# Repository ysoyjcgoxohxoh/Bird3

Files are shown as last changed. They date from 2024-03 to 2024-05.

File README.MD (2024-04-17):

# Bird 3 #

## Introduction ##
This repository attempts to document the specs and operation of the Bird 3 scooter. It provides a PCB design and associated software for a drop-in replacement Bird Brain compatible with the EA00004 and EA00022 brains.

The PCB is designed in KiCad around an ESP32-S3. It is designed to fit into the original enclosure and use the existing LCD, the [TXW154028S0](./Datasheets/TXW154028S0_SPEC.pdf).

More documentation for the scooter is available in the [Wiki](../../wiki).

> [!WARNING]
> This repository is intended for use with legally and ethically acquired scooters only. Not only is stealing scooters a crime, it is also unethical.

## Repository Structure ##
- The `Arduino` directory contains the code to run the scooter.
- The `Datasheets` directory contains datasheets for various components.
- The `PCB` directory contains the PCB design.
  - [Rev 1](./PCB/Bird3Controller_Rev1/Readme.md).
  - [Rev 2](./PCB/Bird3Controller_Rev2/Readme.md).
  - [Rev 3](./PCB/Bird3Controller_Rev3/Readme.md).

## Credits ##
- `Mental_Metalhead` - For lots of back and forth testing the software, providing the 22-pin connector pinout, and for various advice on designing PCBs.
- The folks in the Scooterhacking.org community. (DM me if you wish to be credited directly. You know who you are.)

## Board Renderings - Rev 2 ##
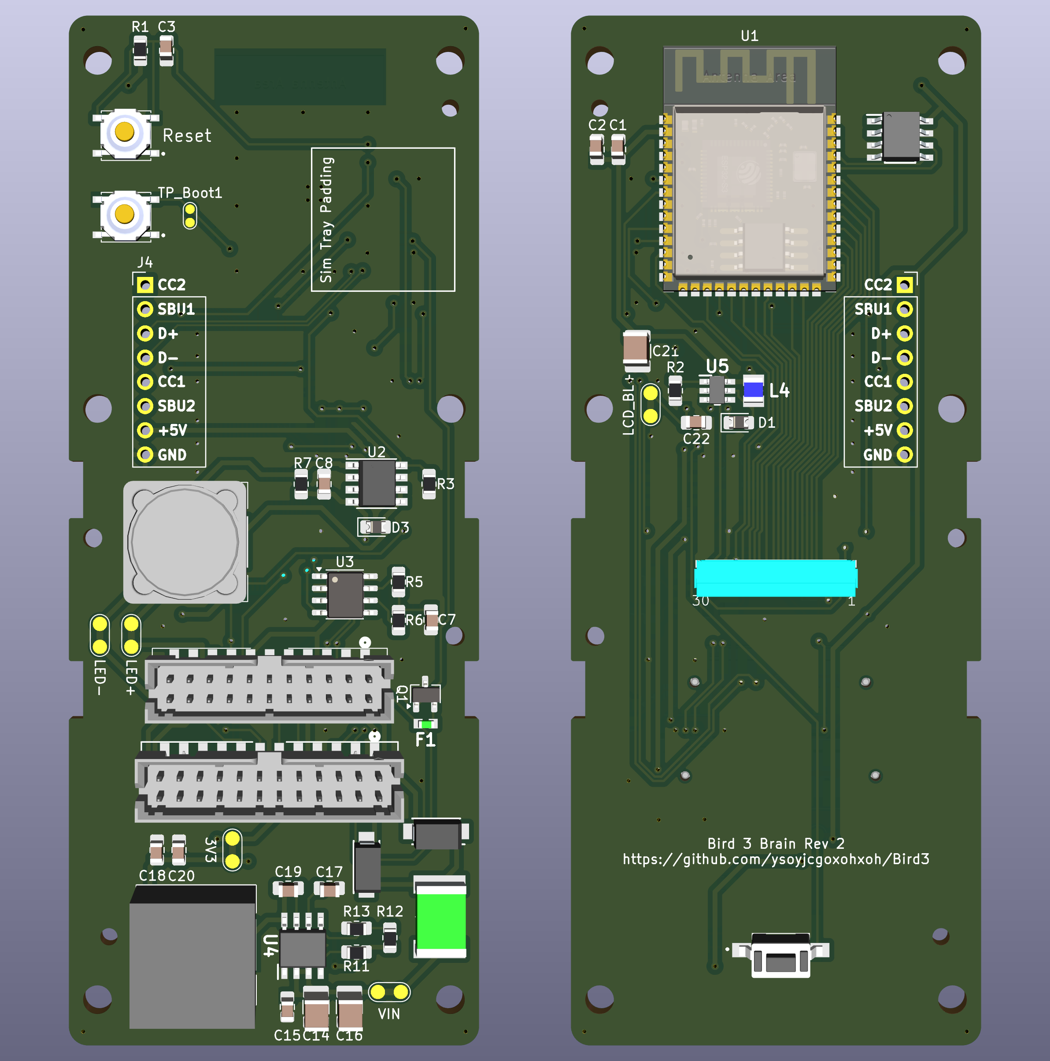
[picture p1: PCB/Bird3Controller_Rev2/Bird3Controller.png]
PCB


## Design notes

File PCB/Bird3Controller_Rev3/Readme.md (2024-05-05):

> [!NOTE]
> This design has been assembled and is working with no errata discovered yet.

## Development ##
This was developed in [KiCad 8](https://www.kicad.org/), a FOSS EDA suite. Most or all of the symbols, footprints, and 3D models have been included in the repo to reduce the chance of broken references.

## Ordering Information ##
[JLCPCB](https://jlcpcb.com/) is a good place from which to order a PCB.
- The gerber files are in the [./plots](plots) folder.
- The Bill of Materials is at [./BOM.csv](BOM.csv).

These JLCPCB settings were used for the order:
| Setting | Value |
|---|---|
| Layers | 2 |
| Dimension | 43 mm * 108 mm |
| PCB Thickness | 1.6 |
| Impedance Control | no |
| Material Type | FR4-Standard TG 135-140 |
| Via Covering | Tented |
| Outer Copper Weight | 1 oz |
| Castellated Holes | no |
| Edge Plating | no |
| Remove Order Number | Specify a location |
| Board Outline Tolerance | ±0.2mm(Regular) |

## Fixes from Rev 2 ##
- TBA

## Improvements from Rev 2 ##
- TBA

## Errata ##
- TBA

## Bill of Materials ##
An interactive BOM generated by [InteractiveHtmlBOM](https://github.com/openscopeproject/InteractiveHtmlBom) is available at [https://html-preview.github.io/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](https://html-preview.github.io/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)

## PDF Schematic ##
A PDF schematic is available at [Bird3Controller.pdf](Bird3Controller.pdf). When opened in a more advanced viewer such as Acrobat Reader, the components are bookmarked, and both components and nets are clickable as shown in this screenshot, making it easy to open the part's datasheet or Mouser.com listing.
PDF Schematic Example

## PNG Schematic ##
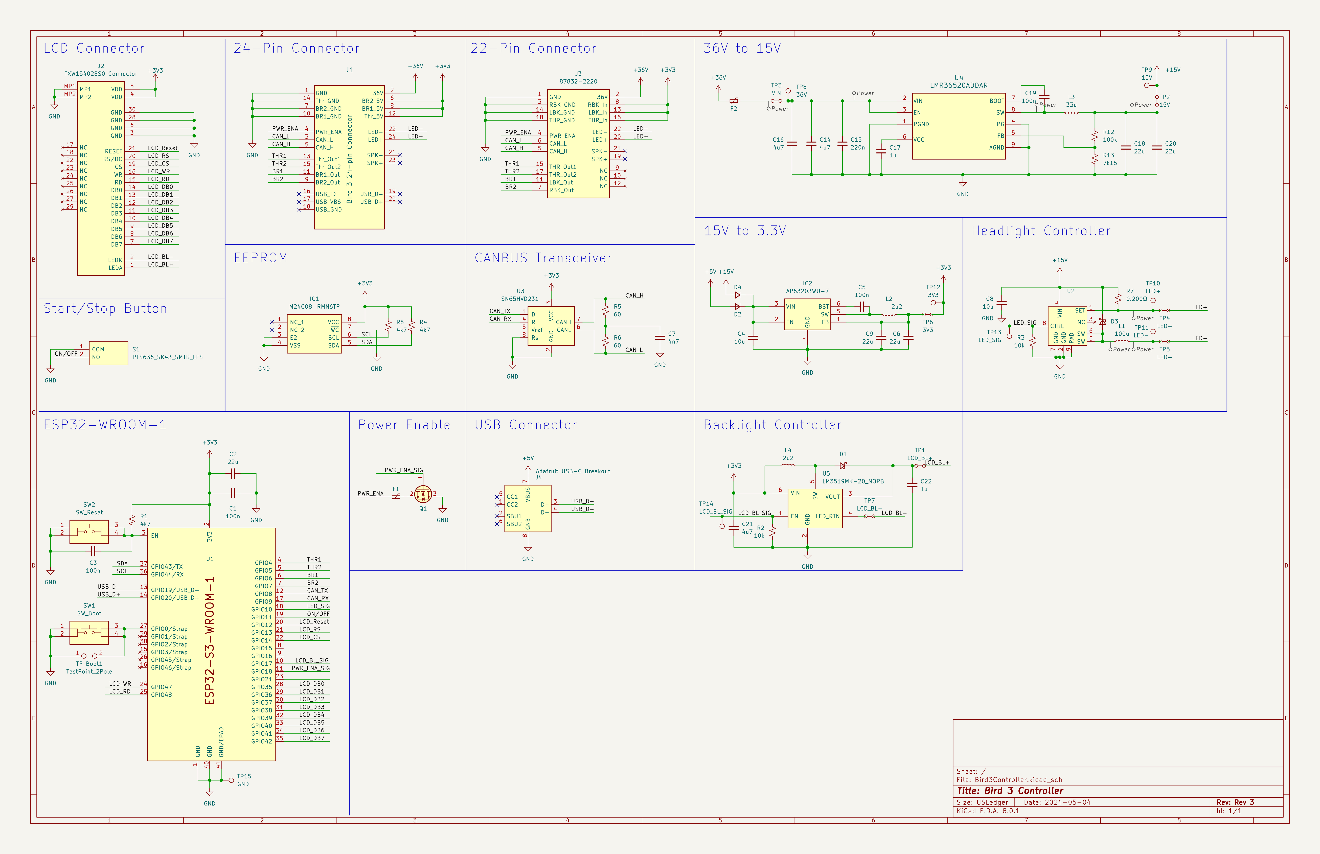
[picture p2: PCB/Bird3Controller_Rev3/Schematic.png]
Schematic


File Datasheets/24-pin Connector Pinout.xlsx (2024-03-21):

Pin Index | Function | Comment | Color
1 | GND | Power Ground | Black
2 | 36V_Perm | Power 36V | Red
3 | CAN_L | CAN Low | Green
4 | PWR_ENA | Ground to Enable Power | Blue
5 | CAN_H | CAN High | Yellow
6 | BR2_5V | Brake 2 Input | Red
7 | BR2_GND | Brake 2 Ground | Black
8 | BR1_5V | Brake 1 Input | Red
9 | BR2_WP | Brake 2 Weak Up | Green
10 | BR1_GND | Brake 1 Ground | Black
11 | BR1_WP | Brake 1 Weak Up | Orange
12 | TR_5V | Throttle Input | Red
13 | TR_WP1 | Throttle Weak Up 1 | Yellow
14 | TR_GND | Throttle Ground | Black
15 | TR_WP2 | Throttle Weak Up 2 | Blue
16 | USB_ID | USB ID | Gray
17 | USB_VBS | USB VBUS | Red
18 | USB_GND | USB Ground | Black
19 | USB_D- | USB D- | White
20 | USB_D+ | USB D+ | Green
21 | SPK- | Speaker Negative | Gray
22 | LED- | LED Negative | White
23 | SPK+ | Speaker Positive | Gray
24 | LED+ | LED Positive | Green

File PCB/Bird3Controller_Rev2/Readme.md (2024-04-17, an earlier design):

> [!NOTE]
> This design doesn't operate the headlight properly.

## Development ##
This was developed in [KiCad 8](https://www.kicad.org/), a FOSS EDA suite. Most or all of the symbols, footprints, and 3D models have been included in the repo to reduce the chance of broken references.

## Ordering Information ##
[JLCPCB](https://jlcpcb.com/) is a good place from which to order a PCB.
- The gerber files are in the [./plots](plots) folder.
- The Bill of Materials is at [./BOM.csv](BOM.csv).

These JLCPCB settings were used for the test order:
| Setting | Value |
|---|---|
| Layers | 2 |
| Dimension | 43 mm* 108 mm |
| PCB Thickness | 1.6 |
| Impedance Control | no |
| Material Type | FR4-Standard TG 135-140 |
| Via Covering | Tented |
| Outer Copper Weight | 1 oz |
| Castellated Holes | no |
| Edge Plating | no |
| Remove Order Number | Specify a location |
| Board Outline Tolerance | ±0.2mm(Regular) |

## Fixes from Rev 1 ##
- Corrected slight inaccuracies in mounting hole locations
- Wired the LCD Connector in the correct direction
- Adjusted LCD mounting to add alignment holes and correct mounting cutout width.
- Moved components interfering with LCD mounting
- Replaced headlight circuit with one that steps down directly from 36V.
- Moved components interfering with LCD
- Increased headlight current setting

## Improvements from Rev 1 ##
- Added 22-pin connector (Credits to `Mental_Metalhead` for the pinout)
- Added EEPROM for durable storage ($0.19 BOM, > 4 million writes)
- Added Mosfet to programatically ground the `PWR_ENA` pin rather than tying it permanently to ground
- Added copper pour to reduce EMI

## Errata ##
- LED Headlight circuit doesn't work due to excessive ratio between VIN (~36V) and VOut (3.0V).

## Board Renderings ##
PCB

## Bill of Materials ##
An interactive BOM generated by [InteractiveHtmlBOM](https://github.com/openscopeproject/InteractiveHtmlBom) is available at [https://html-preview.github.io/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](https://html-preview.github.io/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)

## PDF Schematic ##
A PDF schematic is available at [Bird3Controller.pdf](Bird3Controller.pdf). When opened in a more advanced viewer such as Acrobat Reader, the components are bookmarked, and both components and nets are clickable as shown in this screenshot, making it easy to open the part's datasheet or Mouser.com listing.
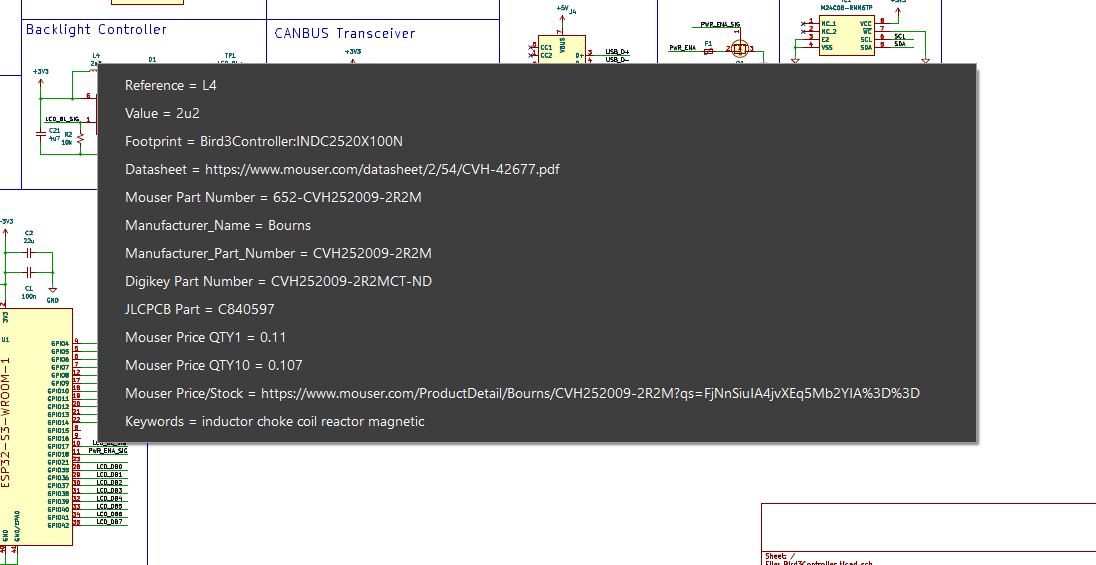
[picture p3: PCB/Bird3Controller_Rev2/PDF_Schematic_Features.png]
PDF Schematic Example


## PNG Schematic ##
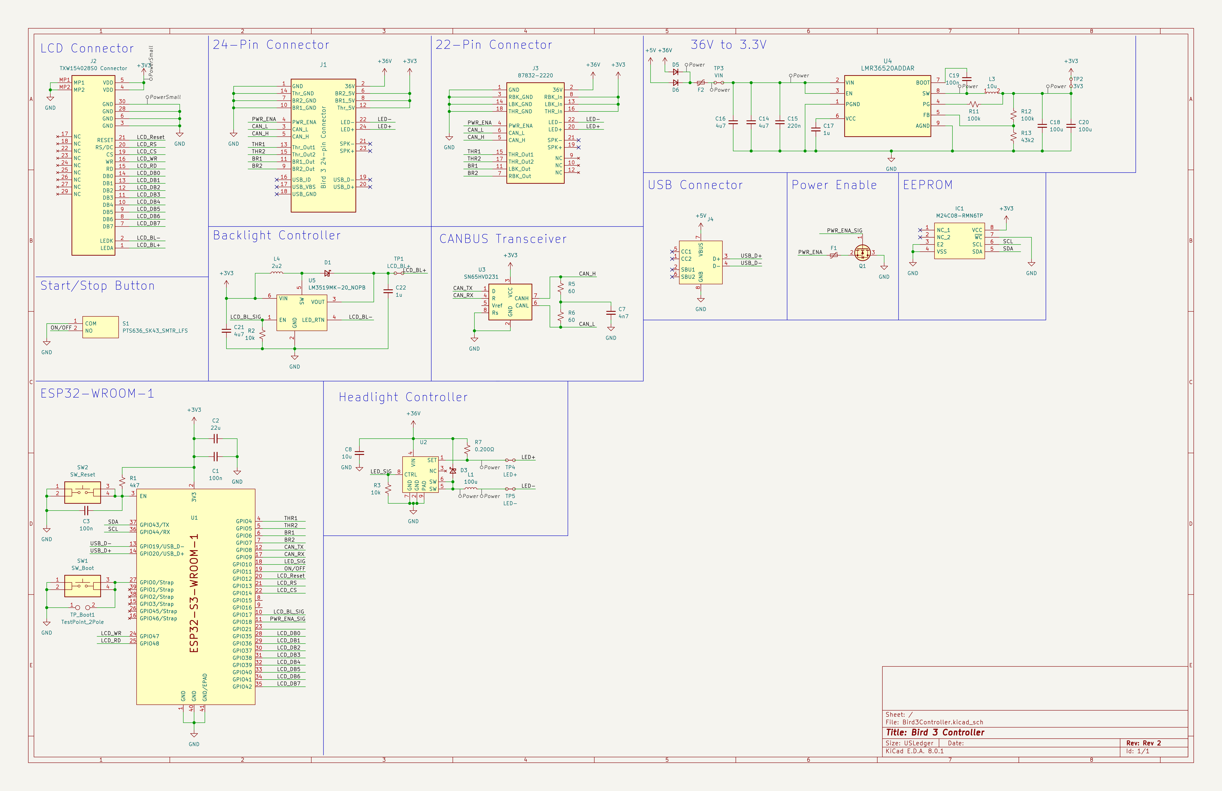
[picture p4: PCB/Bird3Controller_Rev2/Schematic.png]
Schematic


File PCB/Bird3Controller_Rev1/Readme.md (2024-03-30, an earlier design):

> [!NOTE]
> This board does drive the scooter, but it has some issues. This revision is not recommended.

## Errata ##
- Physical
  - The mounting holes are in slightly incorrect locations.
- LCD
  - LCD connector is wired in reverse.
  - The LCD mounting cutouts are not quite big enough, causing a very tight fit when clipping on the LCD.
  - The LCD mounting is missing alignment holes.
  - The data lines to the LCD span two registers, necessitating jumper wires for compatibility with the `TFT_eSPI` library.
- Power
  - There are two 3.3v nets, causing half the board to be unpowered.
  - 3.3v is insufficient for the headlight driver.
- Headlight
  - The headlight driver's current is set too low.
  - The headlight driver's inductor physically interferes with LCD.

## Board Renderings ##
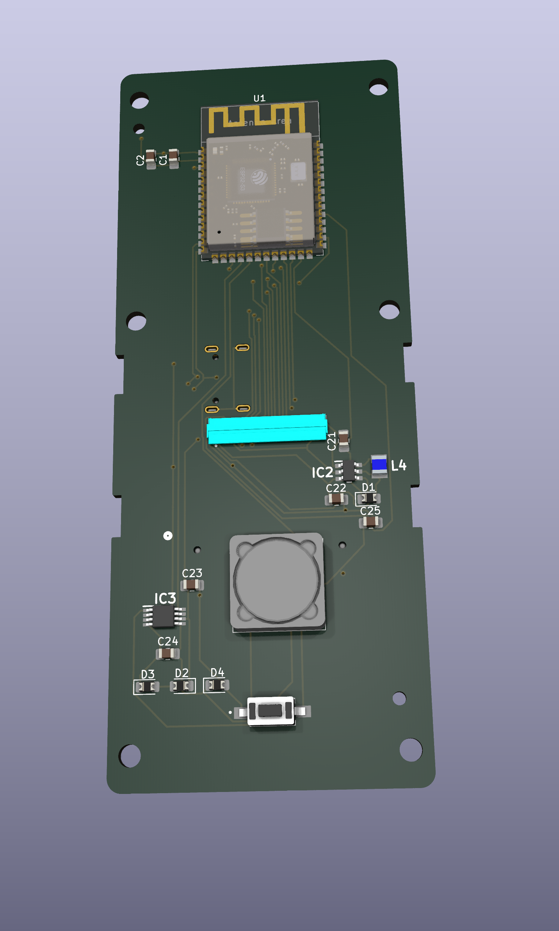
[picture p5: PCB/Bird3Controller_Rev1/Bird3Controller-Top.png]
Top of PCB

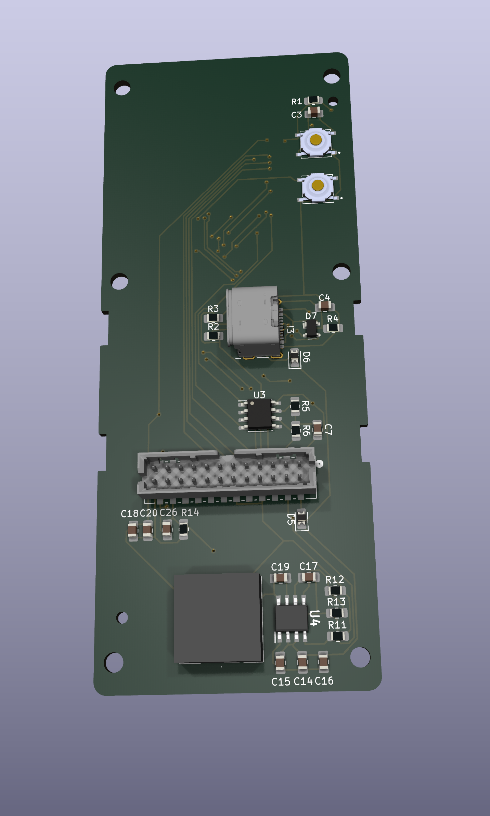
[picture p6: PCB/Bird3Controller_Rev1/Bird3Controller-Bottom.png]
Bottom of PCB


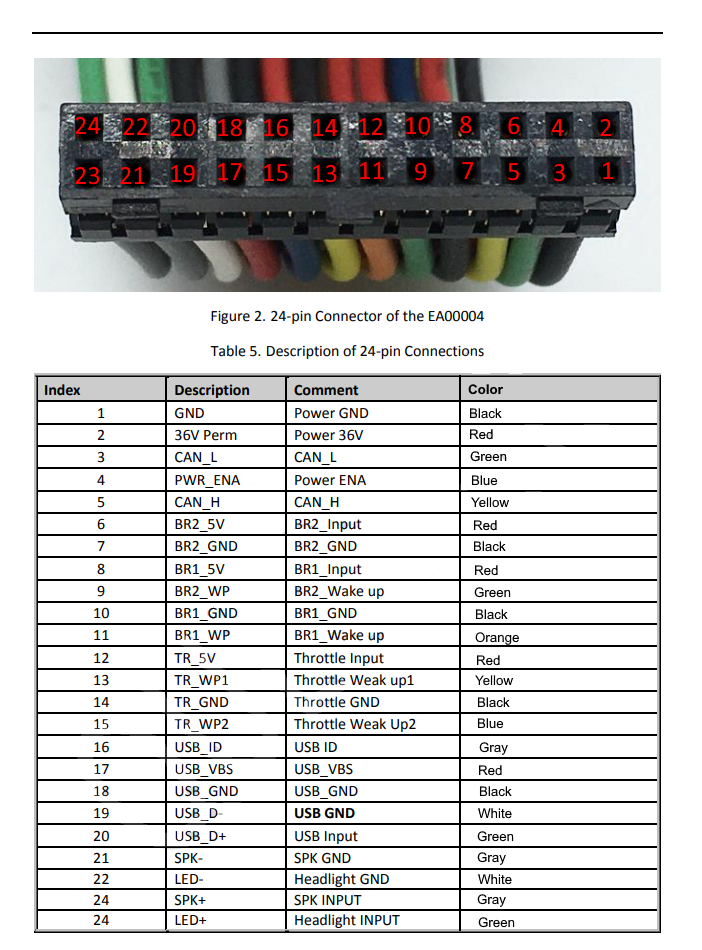
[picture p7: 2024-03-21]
Datasheets/24-pin Connector Pinout.png

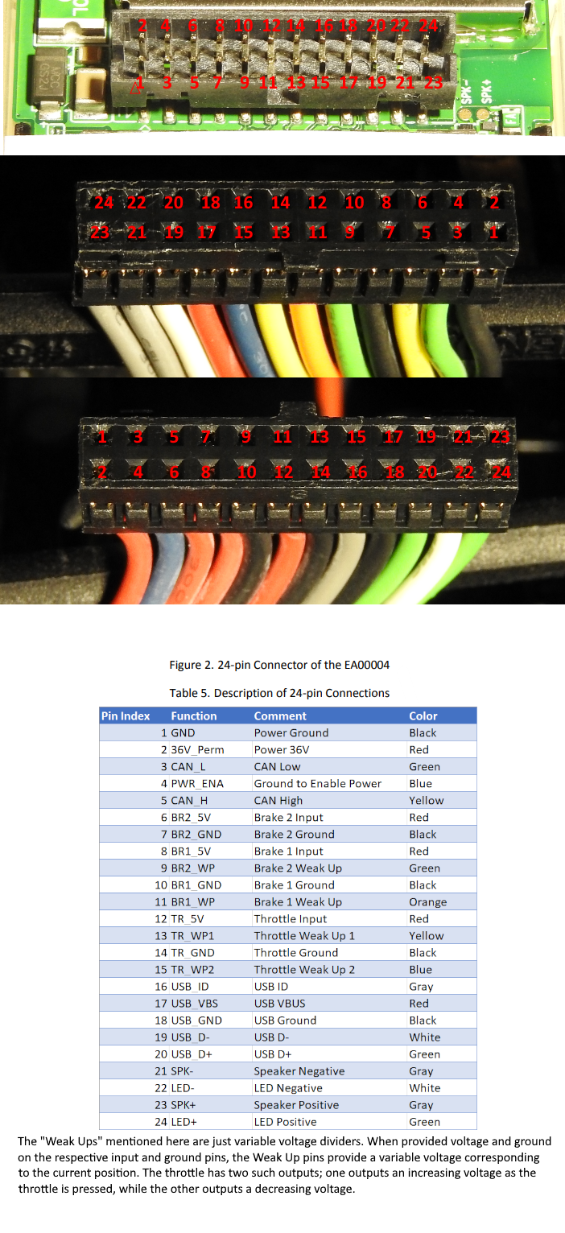
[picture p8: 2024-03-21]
Datasheets/24-pin Connector Pinout Improved.png

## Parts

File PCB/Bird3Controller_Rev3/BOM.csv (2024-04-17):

Reference | Value | Rating | Description | Manufacturer_Name | Manufacturer_Part_Number | Mouser Part Number | Mouser Price/Stock | Qty | Mouser Price QTY1 | Mouser Price QTY10
C1,C3,C5,C19 | 100n | 50V | -- mixed values -- | YAGEO | AC0805JRX7R9BB104 | 603-AC0805JX7R9BB104 | https://www.mouser.com/ProductDetail/YAGEO/AC0805JRX7R9BB104?qs=Znm5pLBrcAKKHbaCmv3b8Q%3D%3D | 4 | 0.10 | 0.065
C2 | 22u | 16V | ESP32 Decoupling | Murata Electronics | GRT21BR61C226ME13L | 81-GRT21BR61C226ME3L | https://www.mouser.com/ProductDetail/Murata-Electronics/GRT21BR61C226ME13L?qs=drgMNd%252BkGPOXePTBixOAtw%3D%3D | 1 | 0.39 | 0.196
C4,C8 | 10u | 25V | 5V/15V Decoupling | Murata Electronics | GRT21BC71E106KE13L | 81-GRT21BC71E106KE13 | https://www.mouser.com/ProductDetail/Murata-Electronics/GRT21BC71E106KE13L?qs=rrS6PyfT74dm3CAfGBwgnw%3D%3D | 2 | 0.35 | 0.199
C6,C9 | 22u | 6.3V | 3V3 Output Filtering | Samsung Electro-Mechanics | CL21A226MQQNNNE | 187-CL21A226MQQNNNE | https://www.mouser.com/ProductDetail/Samsung-Electro-Mechanics/CL21A226MQQNNNE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 | 2 | 0.13 | 0.053
C7 | 4n7 | 50V | CANBUS Split Termination | KYOCERA AVX | 08055C472K4T4A | 581-08055C472K4T4A | https://www.mouser.com/ProductDetail/KYOCERA-AVX/08055C472K4T4A?qs=ykEKLGTiBcx6ErrkugvmMg%3D%3D | 1 | 0.10 | 0.058
C14,C16,C21 | 4u7 | 50V | -- mixed values -- | Samsung Electro-Mechanics | CL32Y475MCIVPNE | 187-CL32B475KBUYNNE | https://www.mouser.com/ProductDetail/Samsung-Electro-Mechanics/CL32B475KBUYNNE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 | 3 | 0.36 | 0.179
C15 | 220n | 50V | 36V Decoupling | Samsung Electro-Mechanics | CL21B224KBFNNNG | 187-CL21B224KBFNNNG | https://www.mouser.com/ProductDetail/Samsung-Electro-Mechanics/CL21B224KBFNNNG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 | 1 | 0.10 | 0.02
C17,C22 | 1u | 50V | LCD Backlight Output Cap | Samsung Electro-Mechanics | CL21B105MBFNNNE | 187-CL21B105MBFNNNE | https://www.mouser.com/ProductDetail/Samsung-Electro-Mechanics/CL21B105MBFNNNE?qs=Znm5pLBrcAIRYa0zX3s5Qw%3D%3D | 2 | 0.10 | 0.027
C18,C20 | 22u | 25V | 15V Output Cap | Samsung Electro-Mechanics | CL21A226MAYNNNE | 187-CL21A226MAYNNNE | https://www.mouser.com/ProductDetail/Samsung-Electro-Mechanics/CL21A226MAYNNNE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 | 2 | 0.25 | 0.115
D1,D3 | D_Schottky_Small | 20V | Freewheeling Diode | KYOCERA AVX | SD0805S020S1R0 | 581-SD0805S020S1R0 | https://www.mouser.com/ProductDetail/KYOCERA-AVX/SD0805S020S1R0?qs=jCA%252BPfw4LHbpkAoSnwrdjw%3D%3D | 2 | 0.32 | 0.252
D2,D4 | GS1J_R1_00001 | 600V | 15V input diode | PANJIT | GS1J_R1_00001 | 241-GS1J_R1_00001 | https://www.mouser.com/ProductDetail/Panjit/GS1J_R1_00001?qs=sPbYRqrBIVmiablUMOUd0Q%3D%3D | 2 | 0.21 | 0.148
F1 | Polyfuse_Small | 60V | PWR_ENA Fuse | Bel Fuse | 0ZCM0001FF2G | 530-0ZCM0001FF2G | https://www.mouser.com/ProductDetail/Bel-Fuse/0ZCM0001FF2G?qs=uwxL4vQweFOSr3rpPGffpA%3D%3D | 1 | 0.19 | 0.16
F2 | 0ZCF0100AF2A | 60V | VIN Fuse | BelFuse | 0ZCF0100AF2A | 530-0ZCF0100AF2A | https://www.mouser.com/ProductDetail/Bel-Fuse/0ZCF0100AF2A?qs=jyPKP7YLNfDyY7GbSCl%252BVQ%3D%3D | 1 | 0.55 | 0.454
IC1 | M24C08-RMN6TP | 5.5V | EEPROM | STMicroelectronics | M24C08-RMN6TP | 511-M24C08-RMN6TP | https://www.mouser.com/ProductDetail/STMicroelectronics/M24C08-RMN6TP?qs=%252B9pWl1iD4MWbThyGTUpSoQ%3D%3D | 1 | 0.19 | 0.175
IC2 | AP63203WU-7 | 32V | 3V3 Switching Regulator | Diodes Incorporated | AP63203WU-7 | 621-AP63203WU-7 | https://www.mouser.com/ProductDetail/Diodes-Incorporated/AP63203WU-7?qs=u16ybLDytRZ1JqxbuLkMJw%3D%3D | 1 | 0.87 | 0.71
J1 | Bird 3 24-pin Connector | 125V, 2A | 24-Pin Connector | Molex | 87832-6123 | 538-87832-6123 | https://www.mouser.com/ProductDetail/Molex/87832-6123?qs=Vr3ZXvgdfhaw8VVGfNJm1w%3D%3D | 1 | 2.05 | 1.79
J2 | TXW154028S0 Connector | 50V, 125mA | LCD Connector | Hirose | FH34SRJ-30S-0.5SH(50) | 798-FH34SRJ30S05SH50 | https://www.mouser.com/ProductDetail/Hirose-Connector/FH34SRJ-30S-0.5SH50?qs=vnk2wBG9e16HHwHqXDE2%252Bg%3D%3D | 1 | 1.24 | 1.05
J3 | 87832-2220 | 125V, 2A | 22-Pin Connector | Molex | 87832-6062 | 538-87832-6062 | https://www.mouser.com/ProductDetail/Molex/87832-6062?qs=yd8XiKYcH9k38KQb4jjFuQ%3D%3D | 1 | 3.27 | 2.98
J4 | Adafruit USB-C Breakout |  | USB-C Breakout | Adafruit | 4090 | 485-4090 | https://www.mouser.com/ProductDetail/Adafruit/4090?qs=2WXlatMagcFDROXrdbBXdg%3D%3D | 1 | 2.95 | 2.95
L1 | 100u | 1.2A, 300mOhms | Headlight Inductor | Bourns | SRR1240-101M | 652-SRR1240-101M | https://www.mouser.com/ProductDetail/Bourns/SRR1240-101M?qs=y9m3SKnhpLNdXTkYqTD5yw%3D%3D | 1 | 0.64 | 0.634
L2 | 2u2 | 2.2A, 90mOhms | 3.3V Inductor | TAIYO YUDEN | MAMK2520H2R2M | 963-MAMK2520H2R2M | https://www.mouser.com/ProductDetail/TAIYO-YUDEN/MAMK2520H2R2M?qs=4JX4e57RtWy63Hw12ZxQ0w%3D%3D | 1 | 0.23 | 0.158
L3 | 33u | 4A, 127.6mOhms | 15V Inductor | Bourns | SRP7050WA-330M | 652-SRP7050WA-330M | https://www.mouser.com/ProductDetail/Bourns/SRP7050WA-330M?qs=9vOqFld9vZUZDPDePm2oBQ%3D%3D | 1 | 0.88 | 0.757
L4 | 2u2 | 1.3A, 80mOhms | Backlight Inductor | Bourns | CVH252009-2R2M | 652-CVH252009-2R2M | https://www.mouser.com/ProductDetail/Bourns/CVH252009-2R2M?qs=FjNnSiuIA4jvXEq5Mb2YIA%3D%3D | 1 | 0.11 | 0.107
Q1 | 2N7002A | 60V, 280mA, 2 Ohms | PWR_ENA Transistor | Diotec | 2N7002A | 637-2N7002A | https://www.mouser.com/ProductDetail/Diotec-Semiconductor/2N7002A?qs=OlC7AqGiEDkkJvTsYoVAvg%3D%3D | 1 | 0.11 | 0.081
R1,R4,R8 | 4k7 | 150v, 125mW | -- mixed values -- | Vishay / Dale | CRCW08054K70JNEA | 71-CRCW0805J-4.7K-E3 | https://www.mouser.com/ProductDetail/Vishay-Dale/CRCW08054K70JNEA?qs=kkyyugUlSrPc3tCn%2F8R5yw%3D%3D | 3 | 0.10 | 0.02
R2,R3 | 10k | 150v, 125mW | -- mixed values -- | Vishay / Dale | CRCW080510K0JNEA | 71-CRCW0805J-10K-E3 | https://www.mouser.com/ProductDetail/Vishay-Dale/CRCW080510K0JNEA?qs=LOX6nxTstiZtNB6HA62jyQ%3D%3D | 2 | 0.10 | 0.019
R5,R6 | 60 | 150v, 500mW | CANBUS Termination | Vishay / Dale | RCS080560R4FKEA | 71-RCS080560R4FKEA | https://www.mouser.com/ProductDetail/Vishay-Dale/RCS080560R4FKEA?qs=AAB0DUhlpksv20rhg0ZRxw%3D%3D | 2 | 0.13 | 0.043
R7 | 0.200Ω | 125mW | Current Sense | TE Connectivity / CGS | RLC73K2AR20FTDF | 279-RLC73K2AR20FTDF | https://www.mouser.com/ProductDetail/TE-Connectivity-CGS/RLC73K2AR20FTDF?qs=9vOqFld9vZWQ3oqbYNtegw%3D%3D | 1 | 0.26 | 0.221
R12 | 100k | 150v, 500mW | 15V Voltage Set Divider | Vishay / Dale | RCS0805100KFKEA | 71-RCS0805100KFKEA | https://www.mouser.com/ProductDetail/Vishay-Dale/RCS0805100KFKEA?qs=NKmfXavxMay%252BH0mbX9hKBw%3D%3D | 1 | 0.13 | 0.063
R13 | 7k15 | 150v, 500mW | 15V Voltage Set Divider | Vishay / Dale | CRCW08057K15FKEAC | 71-CRCW08057K15FKEAC | https://www.mouser.com/ProductDetail/Vishay-Dale/CRCW08057K15FKEAC?qs=E3Y5ESvWgWMF1asUDdVWEg%3D%3D | 1 | 0.11 | 0.029
S1 | PTS636_SK43_SMTR_LFS | 12V, 50mA | Start/Stop Button | C & K COMPONENTS | PTS636 SK43 SMTR LFS | 611-PTS636SK43SMTRLF | https://www.mouser.com/ProductDetail/CK/PTS636-SK43-SMTR-LFS?qs=vLWxofP3U2wsQpQ593zsYw%3D%3D | 1 | 0.16 | 0.148
SW1,SW2 | -- mixed values -- | 12V, 50mA | -- mixed values -- | C & K COMPONENTS | PTS526 SK15 SMTR2 LFS | 611-PTS526SK15SMR2L | https://www.mouser.com/ProductDetail/CK/PTS526-SK15-SMTR2-LFS?qs=UXgszm6BlbF5Ezp94JAQtw%3D%3D | 2 | 0.14 | 0.13
TP8,TP9,TP10,TP11,TP12,TP13,TP14,TP15 | -- mixed values -- |  | test point |  |  |  |  | 8
U1 | ESP32-S3-WROOM-1 | 3.6V | Microcontroller | Espressif Systems | ESP32-S3-WROOM-1-N8R8 | 356-EP32S3WROOM1N8R8 | https://www.mouser.com/ProductDetail/Espressif-Systems/ESP32-S3-WROOM-1-N8R8?qs=7D1LtPJG0i3%2F28hKFavOpQ%3D%3D | 1 | 3.62 | 3.62
U2 | ~ | 60V | Headlight Driver | Diodes | AL8862SP-13 | 621-AL8862SP-13 | https://www.mouser.com/ProductDetail/Diodes-Incorporated/AL8862SP-13?qs=W0yvOO0ixfFVclRYoOMX8w%3D%3D | 1 | 0.93 | 0.748
U3 | SN65HVD231 | 3.6V | CANBUS Driver | Texas Instruments | SN65HVD231DRG4 | 595-SN65HVD231DRG4 | https://www.mouser.com/ProductDetail/Texas-Instruments/SN65HVD231DRG4?qs=QViXGNcIEAtYBoUJPHGedA%3D%3D | 1 | 2.51 | 2.25
U4 | LMR36520ADDAR | 65V | 15V Switching Regulator | Texas Instruments | LMR36520ADDAR | 595-LMR36520ADDAR | https://www.mouser.com/ProductDetail/Texas-Instruments/LMR36520ADDAR?qs=vHuUswq2%252Bsxe%2FiIOFannaw%3D%3D | 1 | 2.72 | 2.39
U5 | LM3519MK-20_NOPB | 5.5V | Backlight Driver | Texas Instruments | LM3519MK-20/NOPB | 926-LM3519MK-20/NOPB | https://www.mouser.com/ProductDetail/Texas-Instruments/LM3519MK-20-NOPB?qs=QbsRYf82W3GbfCEf8%2FkE2A%3D%3D | 1 | 2.02 | 1.72

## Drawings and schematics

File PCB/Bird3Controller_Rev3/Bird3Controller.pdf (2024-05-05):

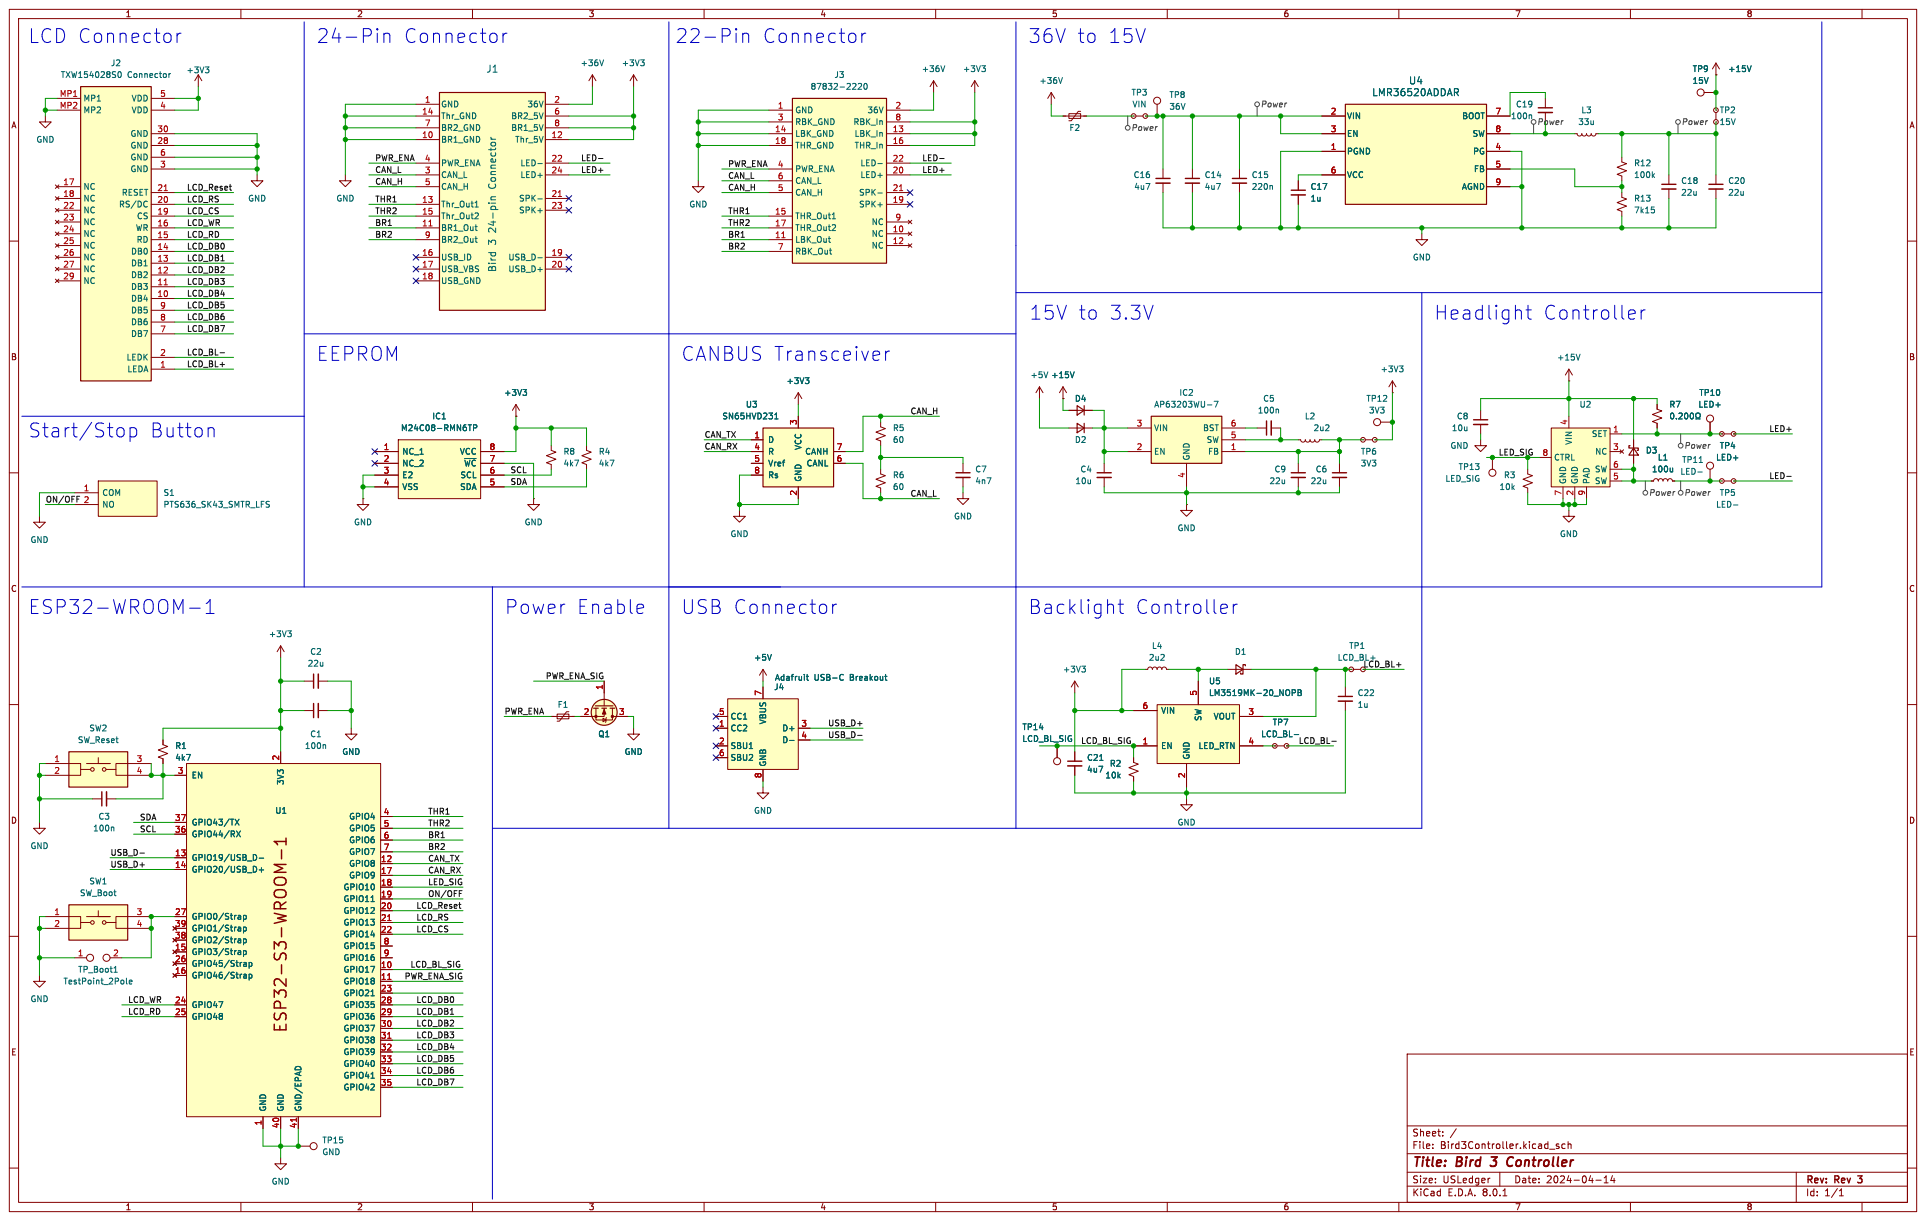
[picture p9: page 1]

Id: 1/1 Title: Bird 3 Controller File: Bird3Controller.kicad_sch Sheet: /

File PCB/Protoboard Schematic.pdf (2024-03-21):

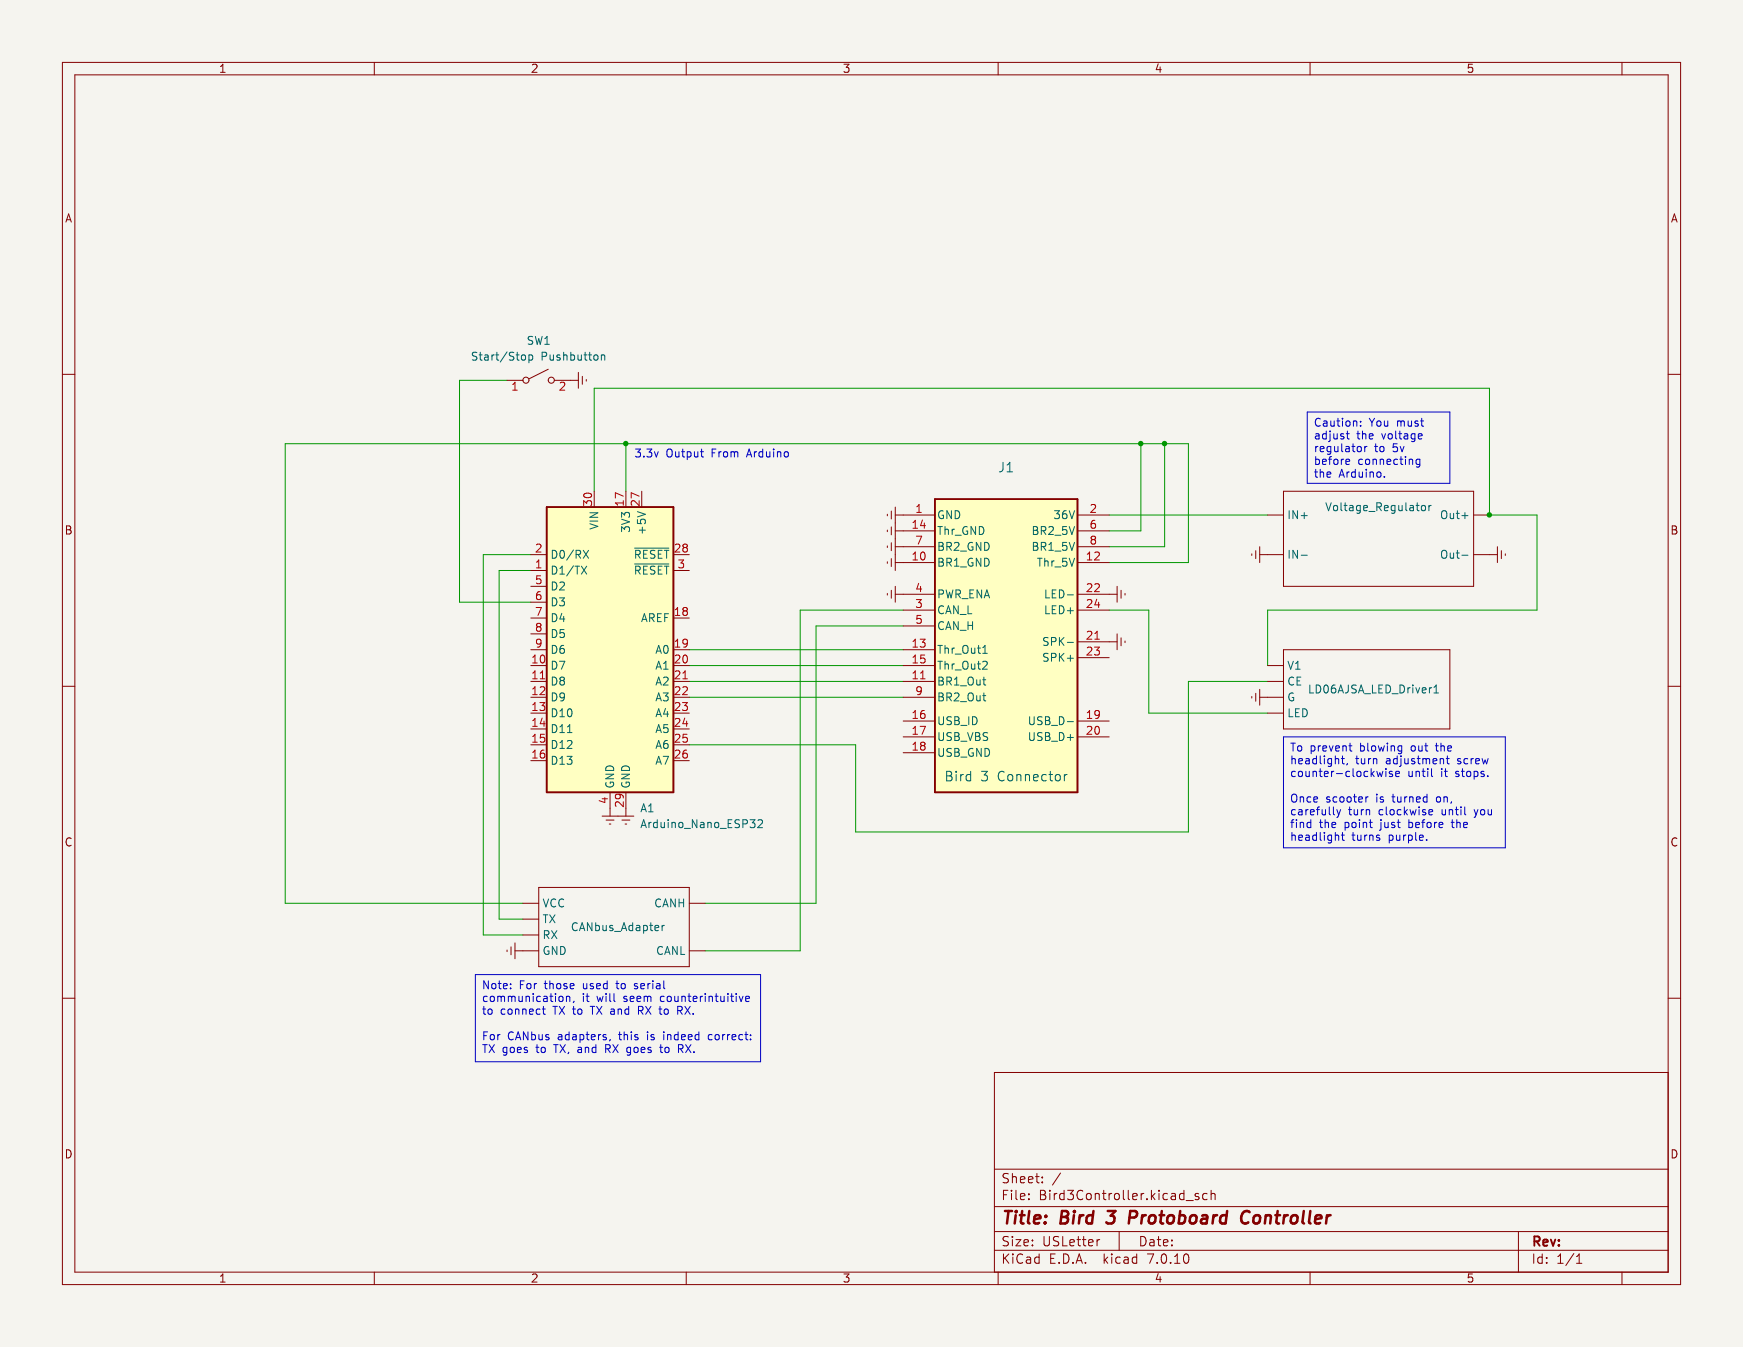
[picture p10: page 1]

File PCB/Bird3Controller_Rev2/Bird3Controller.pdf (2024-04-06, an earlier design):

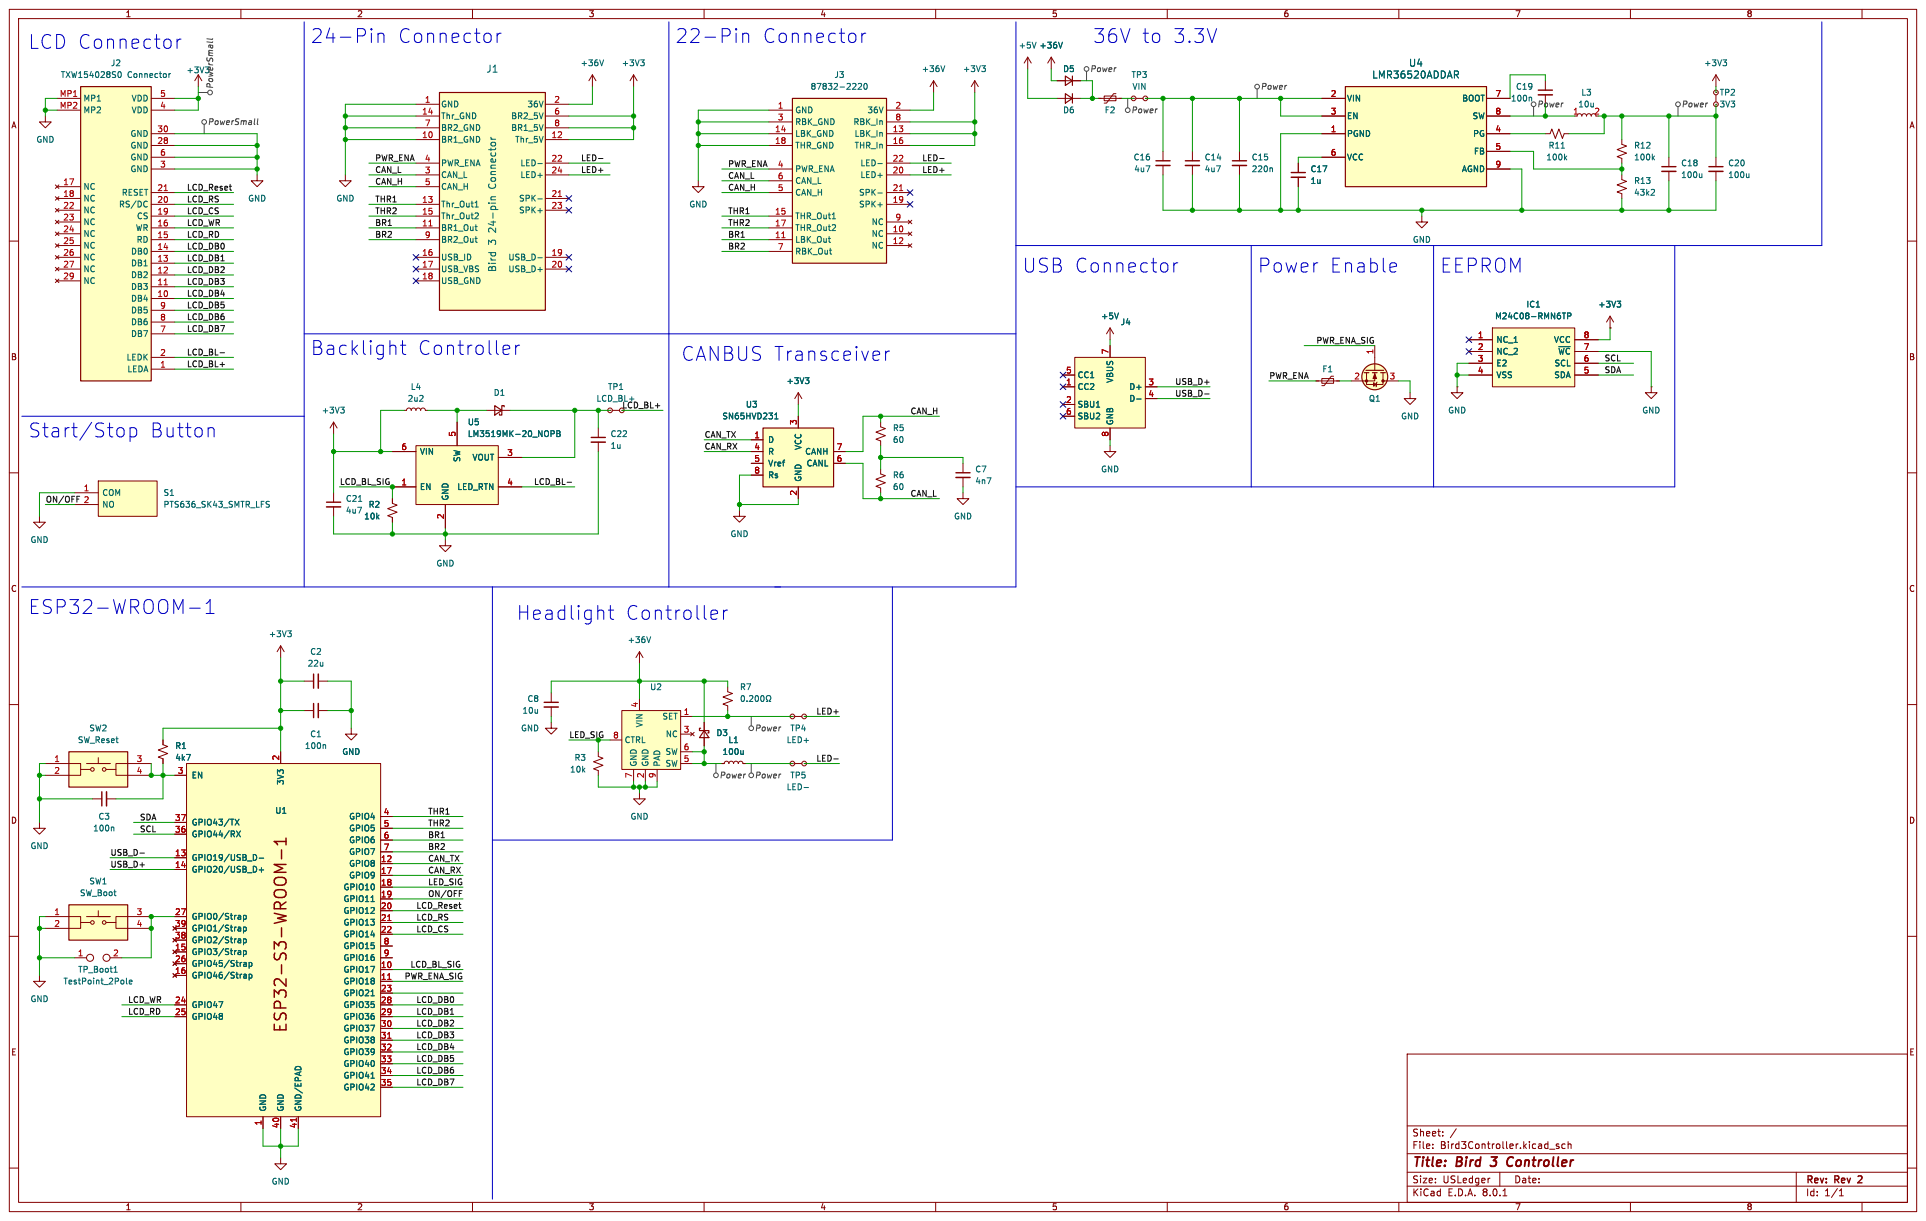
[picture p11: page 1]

Id: 1/1 Title: Bird 3 Controller File: Bird3Controller.kicad_sch Sheet: /

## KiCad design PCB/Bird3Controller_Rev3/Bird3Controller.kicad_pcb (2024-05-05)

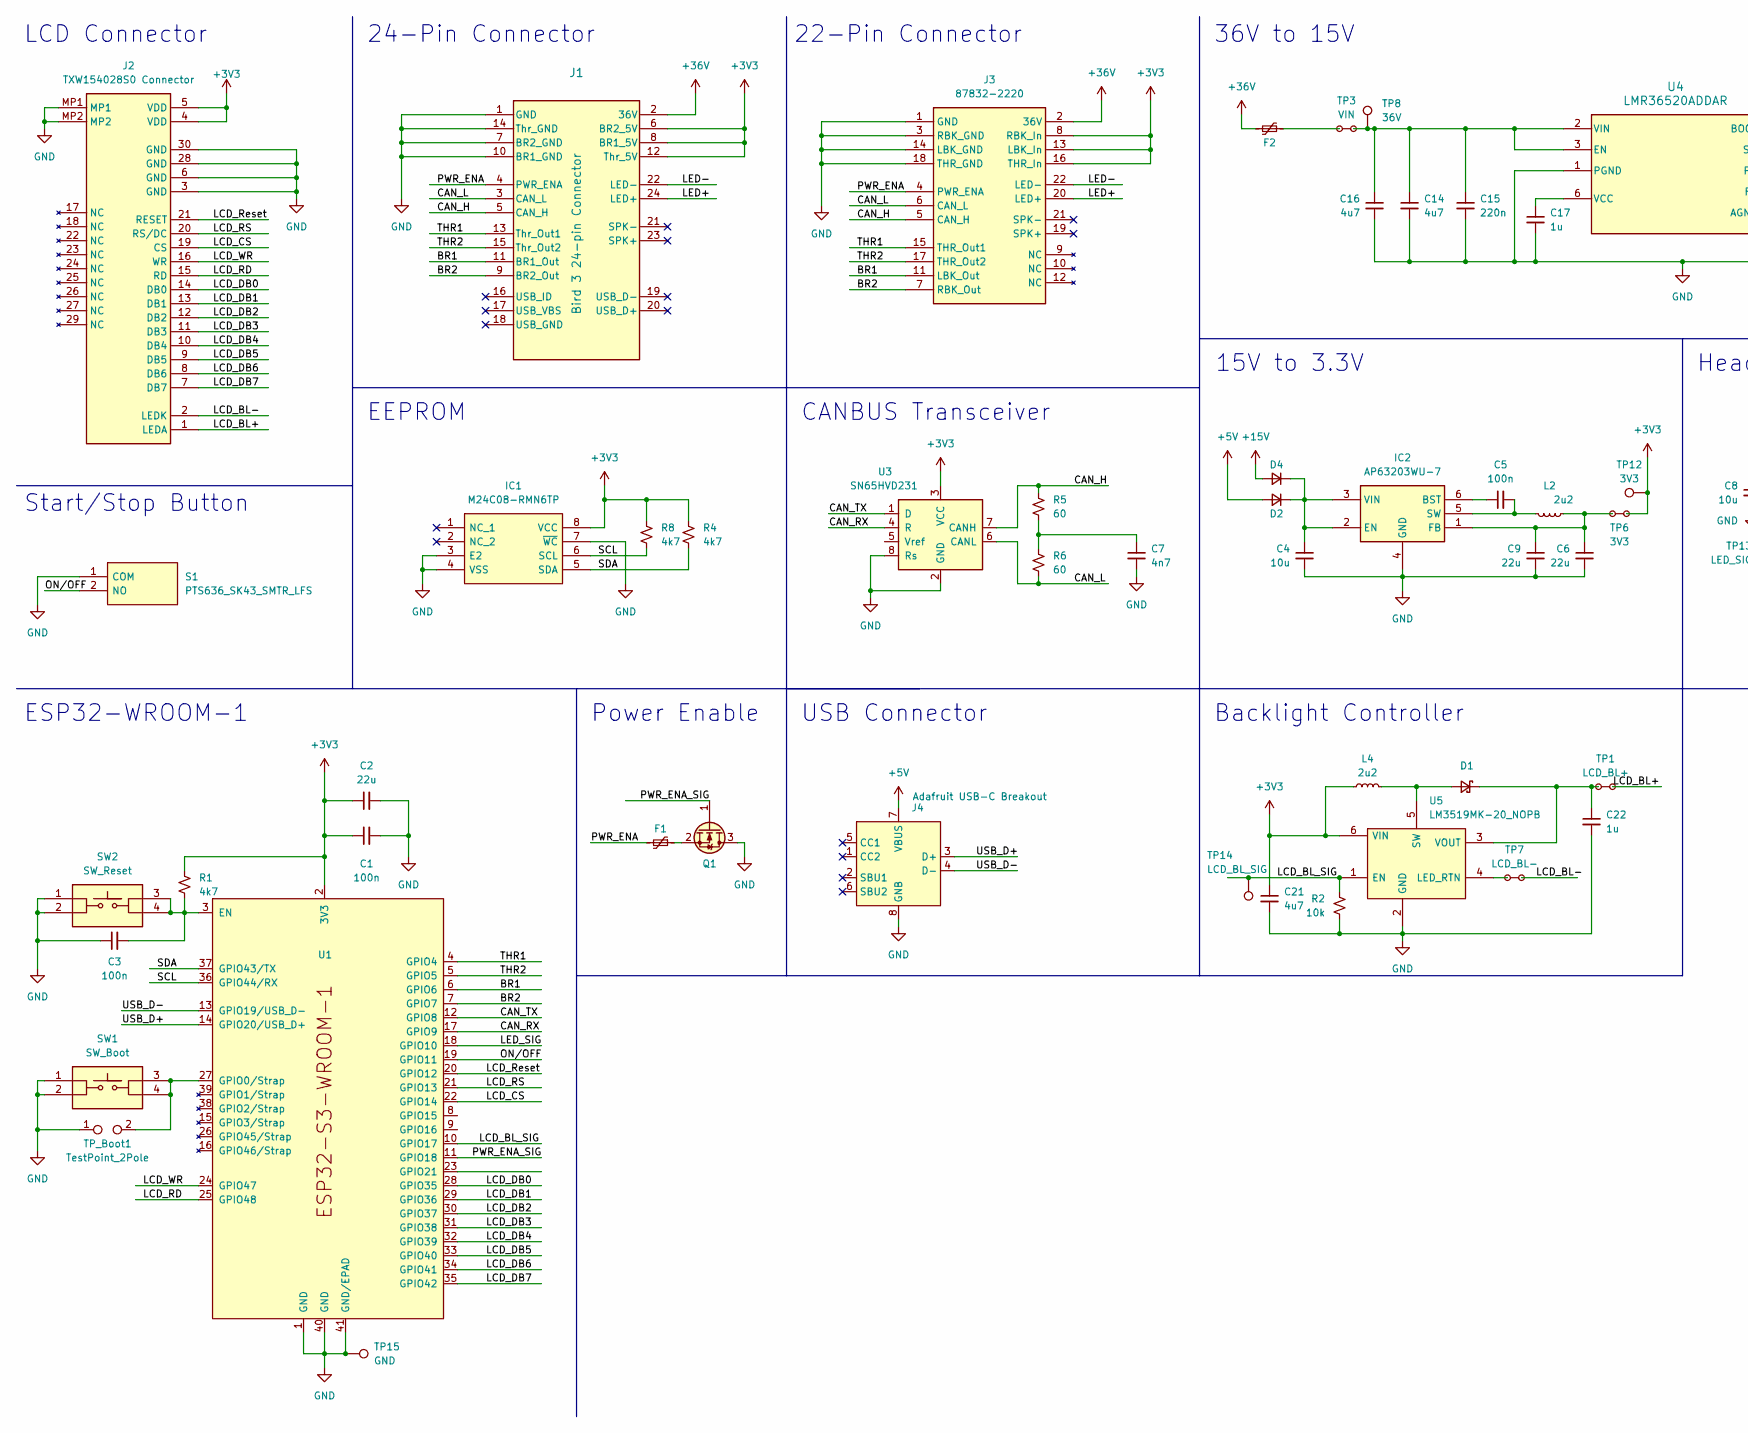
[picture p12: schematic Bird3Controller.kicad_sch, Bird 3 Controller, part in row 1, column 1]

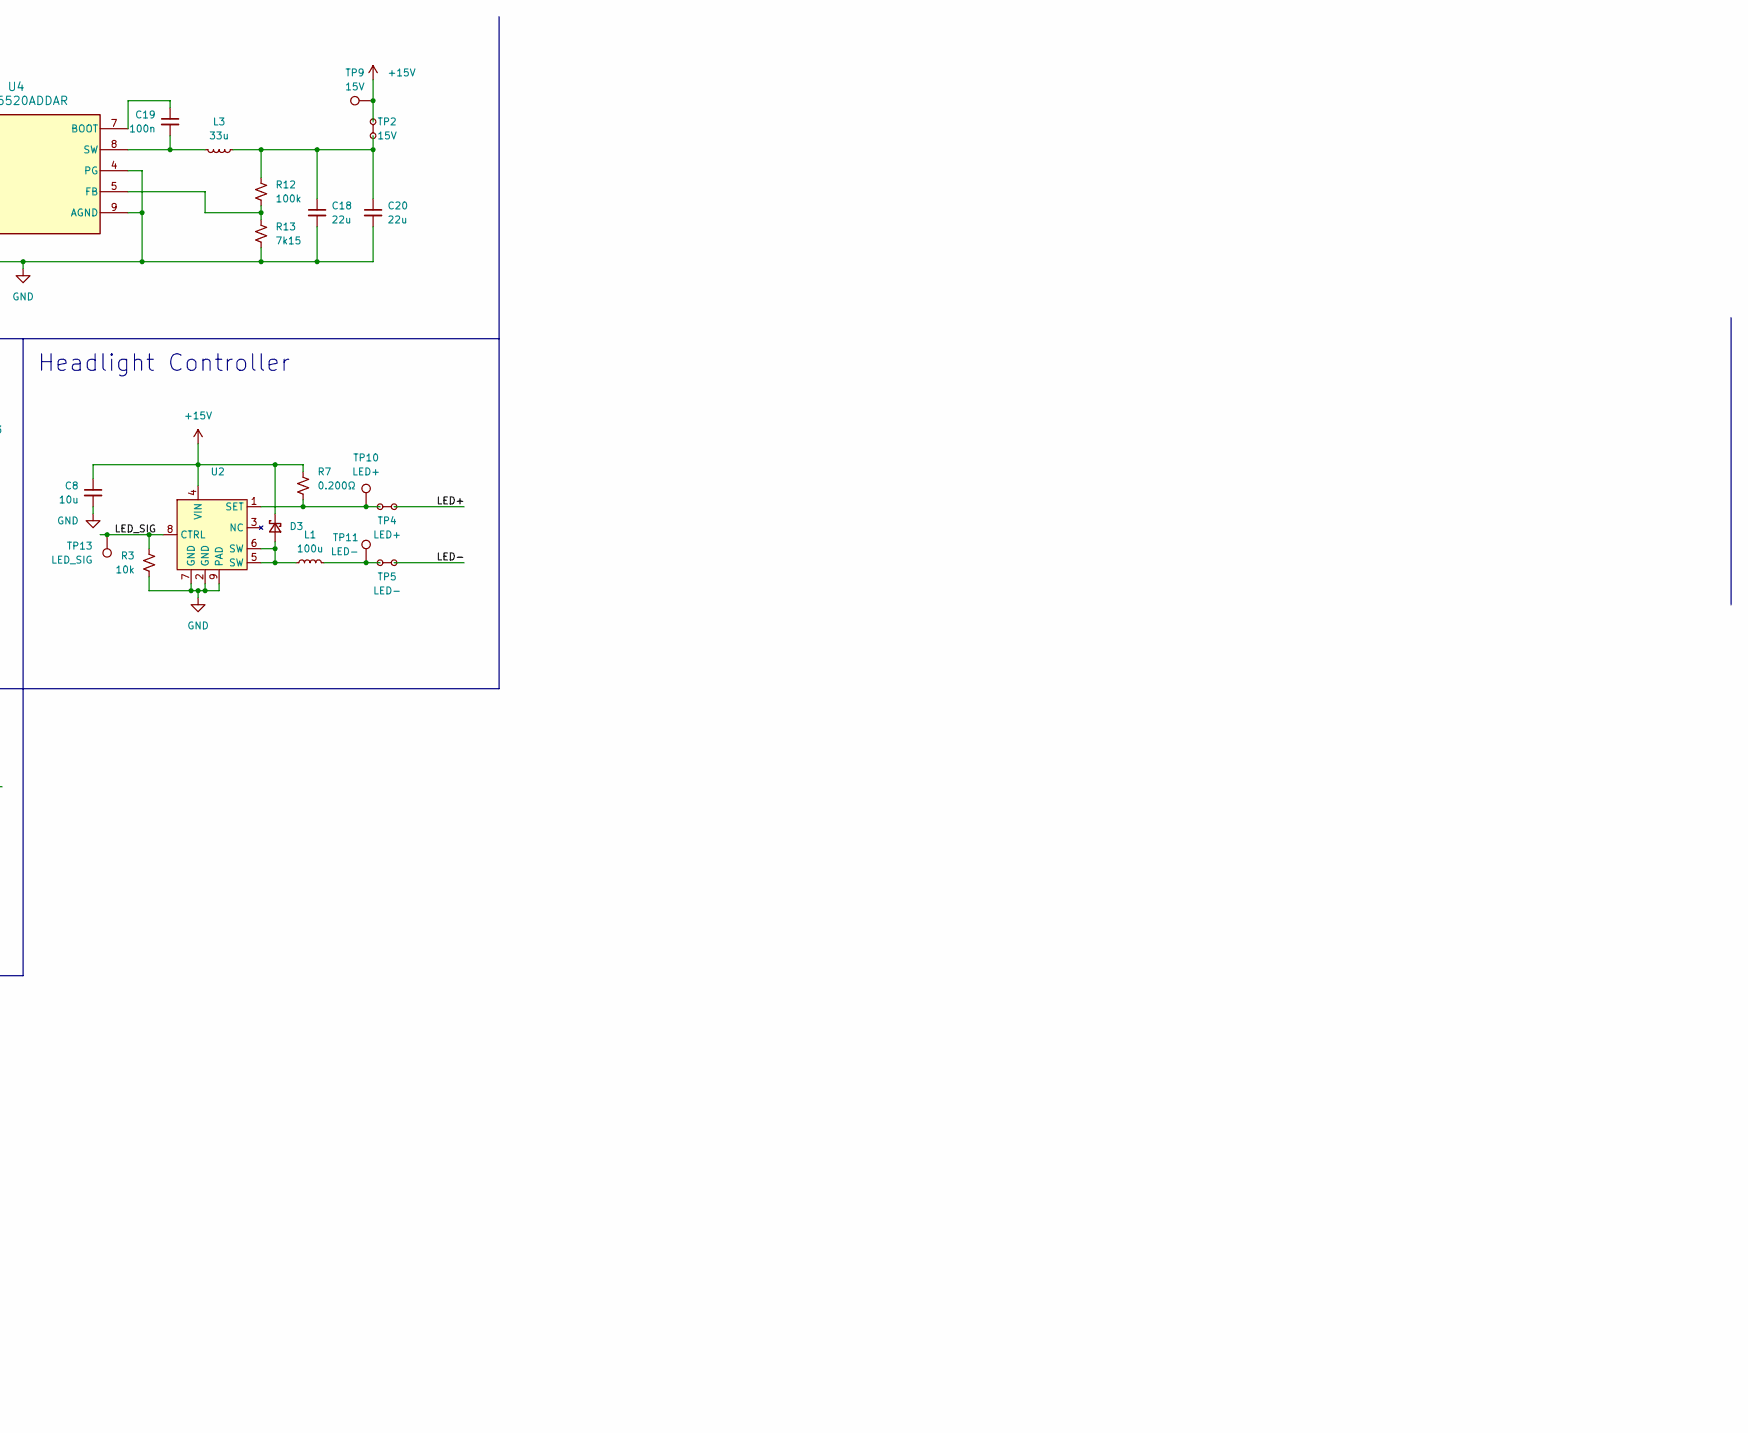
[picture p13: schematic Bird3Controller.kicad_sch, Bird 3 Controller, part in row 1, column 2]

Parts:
C1, C3, C5, C19: 100n; C_0805_2012Metric; Rating 50V; mouser# 581-KGM21NR71H104KT; Digikey Part Number 13-AC0805JRX7R9BB104CT-ND
C2: 22u; C_0805_2012Metric; Rating 16V; mouser# 81-GRT21BR61C226ME3L; Digikey Part Number 490-12383-1-ND
C4, C8: 10u; C_0805_2012Metric; Rating 25V; mouser# 81-GRT21BC71E106KE13; Digikey Part Number 490-GRT21BC71E106KE13LCT-ND
C6, C9: 22u; C_0805_2012Metric; Rating 6.3V; mouser# 187-CL21A226MQQNNNE; Mouser Price QTY1 0.13
C7: 4n7; C_0805_2012Metric; Rating 50V; mouser# 581-08055C472K4T4A; Digikey Part Number 478-KAM21KR71E224KUCT-ND
C14, C16, C21: 4u7; C_1210_3225Metric; Rating 50V; mouser# 187-CL32B475KBUYNNE; Digikey Part Number 1276-CL32Y475KCIVPNECT-ND
C15: 220n; C_0805_2012Metric; Rating 50V; mouser# 187-CL21B224KBFNNNG; Digikey Part Number 478-KAM21KR71E224KUCT-ND
C17, C22: 1u; C_0805_2012Metric; Rating 50V; mouser# 187-CL21B105KBFNNNE; Digikey Part Number 1276-1029-1-ND
C18: 22u; C_0805_2012Metric; Rating 25V; mouser# 187-CL21A226MAYNNWE; Mouser Price QTY1 0.32
C20: 22u; C_0805_2012Metric; Rating 25V; mouser# 187-CL21A226MAYNNWE; Digikey Part Number 1276-CL21A107MQYNNWECT-ND
D1, D3: D_Schottky_Small; D_0805_2012Metric; Rating 20V; mouser# 581-SD0805S020S1R0; Digikey Part Number 478-7800-1-ND
D2, D4: GS1J_R1_00001; DIOM5027X244M; Rating 600V; mouser# 241-GS1J_R1_00001; Digikey Part Number 3757-GS1J_R1_00001CT-ND
F1: Polyfuse_Small; FUSC1607X85N; Rating 60V; mouser# 530-0ZCM0001FF2G; Mouser Price QTY1 0.19
F2: 0ZCF0100AF2A; FUSC7451X170N; Rating 60V; mouser# 530-0ZCF0100AF2A; Mouser Price QTY1 0.55
IC1: M24C08-RMN6TP; SOIC127P600X175-8N; Rating 5.5V; mouser# 511-M24C08-RMN6TP; Mouser Price QTY1 0.19
IC2: AP63203WU-7; AP63203WU7; Rating 32V; mouser# 621-AP63203WU-7; Mouser Price QTY1 0.87
J1: Bird 3 24-pin Connector; CONN_87832-2420_MOL; Rating 125V, 2A; mouser# 538-87832-6123; Digikey Part Number WM18646-ND
J2: TXW154028S0 Connector; FH34SRJ30S05SH50; Rating 50V, 125mA; mouser# 798-FH34SRJ30S05SH50; Digikey Part Number HFT430CT-ND
J3: 87832-2220; 878322220; Rating 125V, 2A; mouser# 538-87832-6062; Mouser Price QTY1 3.27
J4: Adafruit USB-C Breakout; mouser# 485-4090; Mouser Price QTY1 2.95
L1: 100u; SRR1240270M; Rating 1.2A, 300mOhms; mouser# 652-SRR1240-101M; Digikey Part Number SRR1240-101MCT-ND
L2: 2u2; INDC2520X120N; Rating 2.2A, 90mOhms; mouser# 963-MAMK2520H2R2M; Mouser Price QTY1 0.23
L3: 33u; INDPM7973X540N; Rating 4A, 127.6mOhms; mouser# 652-SRP7050WA-330M; Mouser Price QTY1 0.88
L4: 2u2; INDC2520X100N; Rating 1.3A, 80mOhms; mouser# 652-CVH252009-2R2M; Digikey Part Number CVH252009-2R2MCT-ND
Q1: 2N7002A; TSOT-23; Rating 60V, 280mA, 2 Ohms; mouser# 637-2N7002A; Mouser Price QTY1 0.11
R1, R4, R8: 4k7; R_0805_2012Metric; Rating 150v, 125mW; mouser# 71-CRCW0805J-4.7K-E3; Digikey Part Number 541-4.7KACT-ND
R2, R3: 10k; R_0805_2012Metric; Rating 150v, 125mW; mouser# 71-CRCW0805J-10K-E3; Mouser Price QTY1 0.10
R5, R6: 60; R_0805_2012Metric; Rating 150v, 500mW; mouser# 71-RCS080560R4FKEA; Digikey Part Number 541-RCS080560R4FKEACT-ND
R7: 0.200Ω; R_0805_2012Metric; Rating 125mW; mouser# 279-RLC73K2AR20FTDF; Mouser Price QTY1 0.26
R12: 100k; R_0805_2012Metric; Rating 150v, 500mW; mouser# 71-RCS0805100KFKEA; Digikey Part Number 541-2850-1-ND
R13: 7k15; R_0805_2012Metric; Rating 150v, 500mW; mouser# 71-CRCW08057K15FKEAC; Mouser Price QTY1 0.11
S1: PTS636_SK43_SMTR_LFS; PTS636SK43SMTRLFS; Rating 12V, 50mA; mouser# 611-PTS636SK43SMTRLF; Digikey Part Number CKN12311-1-ND
SW1: SW_Boot; PTS526SK15SMTR2LFS; Rating 12V, 50mA; mouser# 611-PTS526SK15SMR2L; Digikey Part Number CKN12221-1-ND
SW2: SW_Reset; PTS526SK15SMTR2LFS; Rating 12V, 50mA; mouser# 611-PTS526SK15SMR2L; Digikey Part Number CKN12221-1-ND
TP1: LCD_BL+; TestPointBridge_2Pads_D1.5mm
TP2: 15V; TestPointBridge_2Pads_D1.5mm
TP3: VIN; TestPointBridge_2Pads_D1.5mm
TP4: LED+; TestPointBridge_2Pads_D1.5mm
TP5: LED-; TestPointBridge_2Pads_D1.5mm
TP6: 3V3; TestPointBridge_2Pads_D1.5mm
TP7: LCD_BL-; TestPointBridge_2Pads_D1.5mm
TP8: 36V; Labeled_TestPoint_1.5mm
TP9: 15V; Labeled_TestPoint_1.5mm
TP10: LED+; Labeled_TestPoint_1.5mm
TP11: LED-; Labeled_TestPoint_1.5mm
TP12: 3V3; Labeled_TestPoint_1.5mm
TP13: LED_SIG; Labeled_TestPoint_1.5mm
TP14: LCD_BL_SIG; Labeled_TestPoint_1.5mm
TP15: GND; Labeled_TestPoint_1.5mm
TP_Boot1: TestPoint_2Pole; TestPoint_2Pads_D1.0mm
U1: ESP32-S3-WROOM-1; Rating 3.6V; mouser# 356-EP32S3WROOM1N8R8; Digikey Part Number 1965-ESP32-S3-WROOM-1-N8R8CT-ND
U2: Diodes_SO-8EP; Rating 60V; mouser# 621-AL8862SP-13; Mouser Price QTY1 0.93
U3: SN65HVD231; SOIC-8_3.9x4.9mm_P1.27mm; Rating 3.6V; mouser# 595-SN65HVD231DRG4; Digikey Part Number 296-15380-1-ND
U4: LMR36520ADDAR; SOIC127P600X170-9N; Rating 65V; mouser# 595-LMR36520ADDAR; Digikey Part Number 296-LMR36520ADDARCT-ND
U5: LM3519MK-20_NOPB; SOT95P280X110-6N; Rating 5.5V; mouser# 926-LM3519MK-20/NOPB; Digikey Part Number 296-43568-1-ND

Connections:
+3V3: C1.1, C2.1, C21.1, IC1.8 (VCC), J1.6 (BR2_5V), J1.8 (BR1_5V), J1.12 (Thr_5V), J2.4 (VDD), J2.5 (VDD), J3.8 (RBK_In), J3.13 (LBK_In), J3.16 (THR_In), L4.1, R1.2, R4.2, R8.1, TP6.2 (1), TP12.1, U1.2 (3V3), U3.3 (VCC), U5.6 (VIN)
+5V: D2.2 (A), J4.7 (VBUS)
+15V: C8.1, D3.1 (K), D4.2 (A), R7.1, TP2.1, TP9.1, U2.4 (VIN)
+36V: F2.1, J1.2 (36V), J3.2 (36V)
/BR1: J1.11 (BR1_Out), J3.11 (LBK_Out), U1.6 (GPIO6)
/BR2: J1.9 (BR2_Out), J3.7 (RBK_Out), U1.7 (GPIO7)
/CAN_H: J1.5 (CAN_H), J3.5 (CAN_H), R5.1, U3.7 (CANH)
/CAN_L: J1.3 (CAN_L), J3.6 (CAN_L), R6.2, U3.6 (CANL)
/CAN_RX: U1.17 (GPIO9), U3.4 (R)
/CAN_TX: U1.12 (GPIO8), U3.1 (D)
/LCD_BL+: J2.1 (LEDA), TP1.1
/LCD_BL-: J2.2 (LEDK), TP7.1
/LCD_BL_SIG: R2.2, TP14.1, U1.10 (GPIO17), U5.1 (EN)
/LCD_CS: J2.19 (CS), U1.22 (GPIO14)
/LCD_DB0: J2.14 (DB0), U1.28 (GPIO35)
/LCD_DB1: J2.13 (DB1), U1.29 (GPIO36)
/LCD_DB2: J2.12 (DB2), U1.30 (GPIO37)
/LCD_DB3: J2.11 (DB3), U1.31 (GPIO38)
/LCD_DB4: J2.10 (DB4), U1.32 (GPIO39)
/LCD_DB5: J2.9 (DB5), U1.33 (GPIO40)
/LCD_DB6: J2.8 (DB6), U1.34 (GPIO41)
/LCD_DB7: J2.7 (DB7), U1.35 (GPIO42)
/LCD_RD: J2.15 (RD), U1.25 (GPIO48)
/LCD_RS: J2.20 (RS/DC), U1.21 (GPIO13)
/LCD_Reset: J2.21 (RESET), U1.20 (GPIO12)
/LCD_WR: J2.16 (WR), U1.24 (GPIO47)
/LED+: J1.24 (LED+), J3.20 (LED+), TP4.2 (1)
/LED-: J1.22 (LED-), J3.22 (LED-), TP5.2 (1)
/LED_SIG: R3.2, TP13.1, U1.18 (GPIO10), U2.8 (CTRL)
/ON/OFF: S1.2 (NO), U1.19 (GPIO11)
/PWR_ENA: F1.2, J1.4 (PWR_ENA), J3.4 (PWR_ENA)
/PWR_ENA_SIG: Q1.1 (G), U1.11 (GPIO18)
/SCL: IC1.6 (SCL), R8.2, U1.36 (GPIO44/RX)
/SDA: IC1.5 (SDA), R4.1, U1.37 (GPIO43/TX)
/THR1: J1.13 (Thr_Out1), J3.15 (THR_Out1), U1.4 (GPIO4)
/THR2: J1.15 (Thr_Out2), J3.17 (THR_Out2), U1.5 (GPIO5)
/USB_D+: J4.3 (D+), U1.14 (GPIO20/USB_D+)
/USB_D-: J4.4 (D-), U1.13 (GPIO19/USB_D-)
GND: C1.2, C2.2, C3.1, C4.2, C6.2, C7.2, C8.2, C9.2, C14.2, C15.2, C16.2, C17.2, C18.2, C20.2, C21.2, C22.2, IC1.3 (E2), IC1.4 (VSS), IC1.7 (~WC), IC2.4 (GND), J1.1 (GND), J1.7 (BR2_GND), J1.10 (BR1_GND), J1.14 (Thr_GND), J2.3 (GND), J2.6 (GND), J2.28 (GND), J2.30 (GND), J2.MP1, J2.MP2, J3.1 (GND), J3.3 (RBK_GND), J3.14 (LBK_GND), J3.18 (THR_GND), J4.8 (GNB), Q1.3 (D), R2.1, R3.1, R13.1, S1.1 (COM), SW1.1, SW1.2, SW2.1, SW2.2, TP15.1, TP_Boot1.1, U1.1 (GND), U1.40 (GND), U1.41 (GND/EPAD), U2.2 (GND), U2.7 (GND), U2.9 (PAD), U3.2 (GND), U3.8 (Rs), U4.1 (PGND), U4.4 (PG), U4.9 (AGND), U5.2 (GND)
unnamed: C7.1, R5.2, R6.1
unnamed: C18.1, C20.1, L3.2, R12.2, TP2.2 (1)
unnamed: D1.2 (A), L4.2, U5.5 (SW)
unnamed: C22.1, D1.1 (K), TP1.2 (1), U5.3 (VOUT)
unnamed: C4.1, D2.1 (K), D4.1 (K), IC2.2 (EN), IC2.3 (VIN)
unnamed: D3.2 (A), L1.1, U2.5 (SW), U2.6 (SW)
unnamed: F2.2, TP3.2 (1)
unnamed: C5.1, IC2.6 (BST)
unnamed: C6.1, C9.1, IC2.1 (FB), L2.2, TP6.1
unnamed: C5.2, IC2.5 (SW), L2.1
unnamed: L1.2, TP5.1, TP11.1
unnamed: F1.1, Q1.2 (S)
unnamed: C3.2, R1.1, SW2.3, SW2.4, U1.3 (EN)
unnamed: SW1.3, SW1.4, TP_Boot1.2, U1.27 (GPIO0/Strap)
unnamed: R7.2, TP4.1, TP10.1, U2.1 (SET)
unnamed: C19.1, U4.7 (BOOT)
unnamed: C14.1, C15.1, C16.1, TP3.1, TP8.1, U4.2 (VIN), U4.3 (EN)
unnamed: R12.1, R13.2, U4.5 (FB)
unnamed: C19.2, L3.1, U4.8 (SW)
unnamed: C17.1, U4.6 (VCC)
unnamed: TP7.2 (1), U5.4 (LED_RTN)

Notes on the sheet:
22-Pin Connector
Headlight Controller
15V to 3.3V
EEPROM
36V to 15V
Power Enable
ESP32-WROOM-1
CANBUS Transceiver
24-Pin Connector
LCD Connector
Backlight Controller
Start/Stop Button
USB Connector

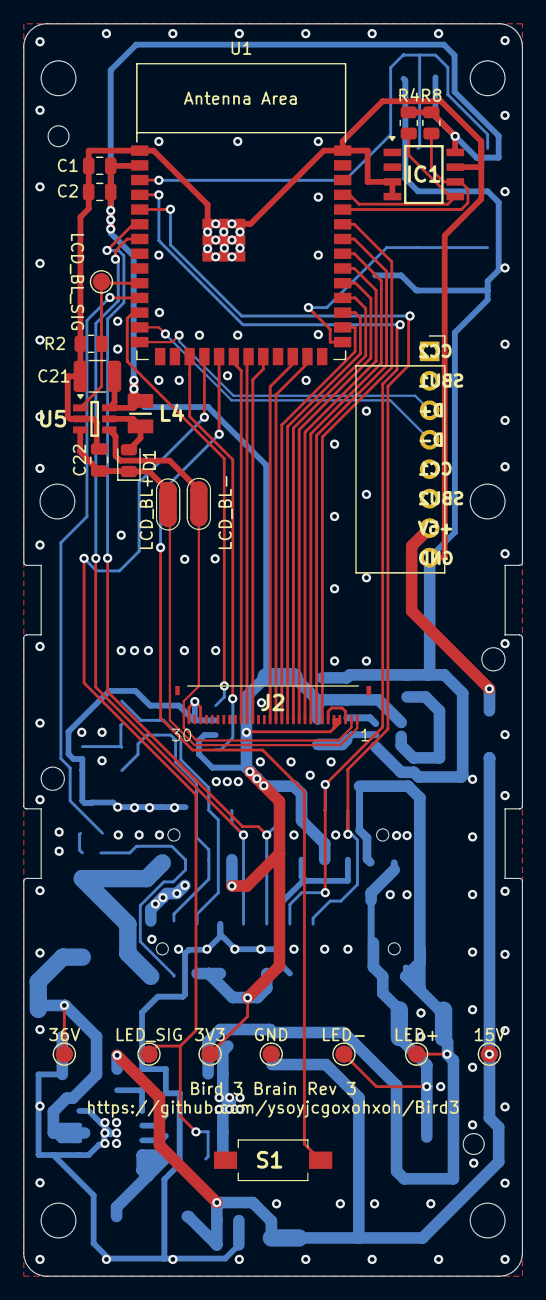
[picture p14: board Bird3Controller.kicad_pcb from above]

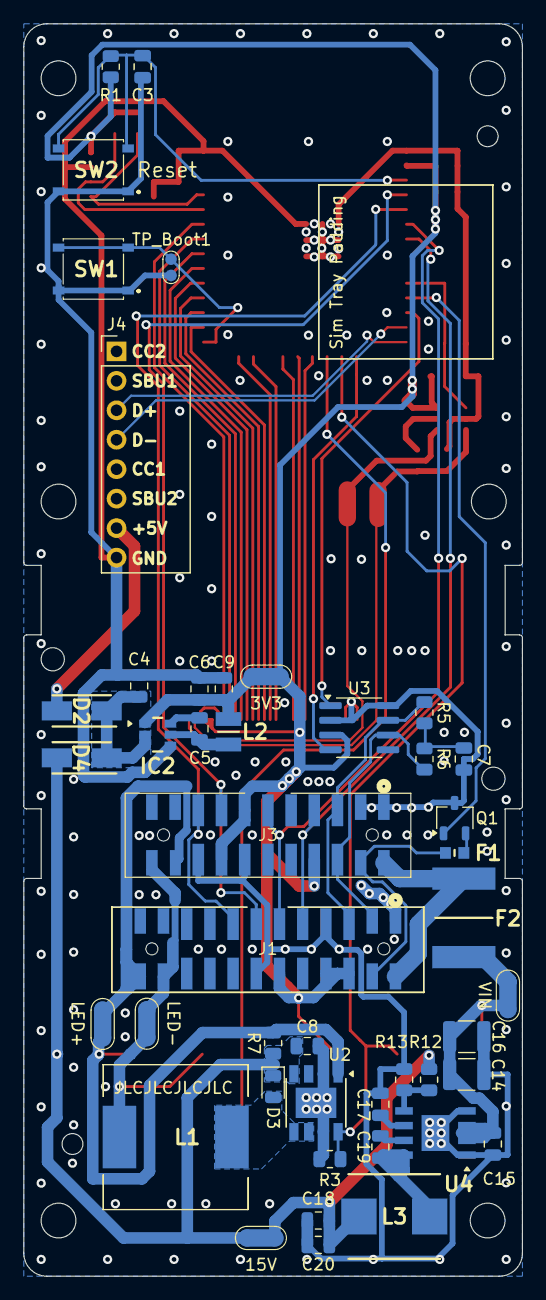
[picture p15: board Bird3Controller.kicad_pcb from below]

Board: 2 copper layers, 43.0 x 108.0 mm, 69 parts (45 on the bottom side), 60 nets.

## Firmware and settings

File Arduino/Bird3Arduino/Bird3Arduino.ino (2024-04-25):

//#define Arduino_Nano_ESP32
//#define ESP32BirdBrainRev1
#define ESP32BirdBrainRev2

#include "driver/twai.h"  // ESP32 Driver
#include "ADebouncer.h"   // ADebouncer 1.1.0 by MicroBeaut
#include "BirdBrainRemoteXY.h"

void IRAM_ATTR Timer0_ISR(void);

#ifdef Arduino_Nano_ESP32

// Communication Pins
#define CAN_RX_PIN 44  // RX0
#define CAN_TX_PIN 43  // TX1

// Inputs
#define THROTTLEA_PIN A0   // TR_WP1 - Increases as throttle is pressed, Connector Pin 13
#define THROTTLEB_PIN A1   // TR_WP2 - Decreases as throttle is pressed, Connector Pin 15
#define BRAKEL_PIN A2      // Brake #2, Rear Brake, Connector Pin #11
#define BRAKER_PIN A3      // Brake #1, Front Brake, Connector Pin #9
#define START_STOP_PIN D3  // Input

// Outputs
#define HEADLIGHT_PIN A6  // Output to LED Driver. PWM in future, but for now, just on/off

// Set up the rgb led names (Arduino Nano ESP32)
#define ledR 14
#define ledG 15
#define ledB 16
#endif

#ifdef ESP32BirdBrainRev1

// Communication Pins
#define CAN_RX_PIN     9   // ESP Pin 17
#define CAN_TX_PIN     8   // ESP Pin 12

// Inputs
#define THROTTLEA_PIN  4   // ESP Pin 4  - TR_WP1 - Increases as throttle is pressed, Connector Pin 13
#define THROTTLEB_PIN  5   // ESP Pin 5  - TR_WP2 - Decreases as throttle is pressed, Connector Pin 15
#define BRAKEL_PIN     6   // ESP Pin 6  - Brake #2, Rear Brake, Connector Pin #11
#define BRAKER_PIN     7   // ESP Pin 7  - Brake #1, Front Brake, Connector Pin #9
#define START_STOP_PIN 11  // ESP Pin 19 - Input

// Outputs
#define HEADLIGHT_PIN  10  // ESP Pin 18 - Output to LED Driver. PWM in future, but for now, just on/off
#define LCD_BL_SIG     48  // ESP Pin 25 - Output to LCD Backlight driver

// LCD Pins
// Changes must be made in ..\libraries\TFT_eSPI\User_Setup.h starting at line 254
#define TFT_RST        12  // ESP Pin 20
#define TFT_DC         13   // ESP Pin 21; LCD RS/DC
#define TFT_CS         14   // ESP Pin 22
#define TFT_WR         15   // ESP Pin 08
#define TFT_RD         16   // ESP Pin 09
#define TFT_D0         39   // Moved to ESP Pin 32  //17 // ESP Pin 10
#define TFT_D1         40   // Moved to ESP Pin 33  //18 // ESP Pin 11
#define TFT_D2         41   // Moved to ESP Pin 34  //21 // ESP Pin 23
#define TFT_D3         35   // ESP Pin 28
#define TFT_D4         36   // ESP Pin 29
#define TFT_D5         37   // ESP Pin 30
#define TFT_D6         38   // ESP Pin 31
#define TFT_D7         47   // ESP Pin 24

#define TFT_Rotation   0

#endif


#ifdef ESP32BirdBrainRev2

// Communication Pins
#define CAN_RX_PIN     9   // ESP Pin 17
#define CAN_TX_PIN     8   // ESP Pin 12
#define I2C_SDA        43  // ESP Pin 37 - I2C Serial Data Line
#define I2C_SCL        44  // ESP Pin 36 - I2C Serial Clock Line

// Inputs
#define THROTTLEA_PIN  4   // ESP Pin 4  - TR_WP1 - Increases as throttle is pressed, Connector Pin 13
#define THROTTLEB_PIN  5   // ESP Pin 5  - TR_WP2 - Decreases as throttle is pressed, Connector Pin 15
#define BRAKEL_PIN     6   // ESP Pin 6  - Brake #2, Rear Brake, Connector Pin #11
#define BRAKER_PIN     7   // ESP Pin 7  - Brake #1, Front Brake, Connector Pin #9
#define START_STOP_PIN 11  // ESP Pin 19 - Input

// Outputs
#define HEADLIGHT_PIN  10  // ESP Pin 18 - Output to LED Driver. PWM in future, but for now, just on/off
#define LCD_BL_SIG     17  // ESP Pin 10 - Output to LCD Backlight driver
#define PWR_ENA_SIG    18  // ESP Pin 11 - Output to PWR_ENA mosfet. Pulling this high connects the PWR_ENA pin on the Bird connector to ground, waking up the ESC and possibly the BMS.

// LCD Pins
// Changes must be made in ..\libraries\TFT_eSPI\User_Setup.h starting at line 254
#define TFT_RST        12  // ESP Pin 20
#define TFT_DC         13  // ESP Pin 21; LCD RS/DC
#define TFT_CS         14  // ESP Pin 22
#define TFT_WR         47  // ESP Pin 24
#define TFT_RD         48  // ESP Pin 25
#define TFT_D0         35  // ESP Pin 28
#define TFT_D1         36  // ESP Pin 29
#define TFT_D2         37  // ESP Pin 30
#define TFT_D3         38  // ESP Pin 31
#define TFT_D4         39  // ESP Pin 32
#define TFT_D5         40  // ESP Pin 33
#define TFT_D6         41  // ESP Pin 34
#define TFT_D7         42  // ESP Pin 35

#define TFT_Rotation   2

#endif

#ifdef TFT_RST
// If the LCD pins have been defined, then assume we're using the LCD and import/define the relevant stuff

#include "TFT_eSPI.h" // TFT_eSPI 2.5.43 by Bodmer
#include "OpenFontRender.h" // Git Submodule
#include "NotoSans_Bold.h"
#include "LockIconFont.h"

// Variables used only if LCD is used.
TFT_eSPI tft = TFT_eSPI();
// Drawing directly to the display introduces a lot of flickering. Using a Sprite as an intermediary eliminates the flickering.
TFT_eSprite screen = TFT_eSprite(&tft);
OpenFontRender noto;
OpenFontRender icons;
#endif



// Whether the CANbus driver and the associated 2ms timer has been initialized.
// When paired with certain CAN chips (knockoffs of the TJA1050), the ESP32 crashes repeatedly if
// not connected to a live CANbus, preventing us from debugging or programming it. This solution
// delays initialization of the CANbus and the timer until the user presses the button once.
static bool driver_installed = false;

volatile uint16_t throttlePos = 0;
typedef enum {
  LockWheel = 1,
  Disabled = 2,
  Idle = 3,
  Running = 4
} ScooterStates;

extern volatile ScooterStates scooterState = Disabled;

// uint32 should suffice for this. Incremented once per second, this will take 136 years to overflow.
volatile uint32_t uptime = 1;
volatile int16_t currentSpeed = 0;
#define TireDiameterMM 254.0  // OE tires are 10x2.5
#define SpeedToKPH TireDiameterMM * 3.141592653 * 60.0 / 1000.0 / 1000.0
#define SpeedToMPH TireDiameterMM * 3.141592653 * 60.0 / 25.4 / 12.0 / 5280.0

ADebouncer StartStopDebouncer;

// Stores the uptime at which there was no longer a request for BMS output. This is used to delay shutting down the BMS, as it doesn't like short shutdowns.
volatile uint32_t bmsOutputDisableRequestedUptime = 0;
uint8_t BMSOutputEnable[8] = { 0x00, 0x01, 0x00, 0x00, 0x00, 0x00, 0x00, 0x00 };
uint8_t BMSOutputDisable[8] = { 0x00, 0x00, 0x00, 0x00, 0x00, 0x00, 0x00, 0x00 };
uint8_t RearLightEnable[8] = { 0x01, 0x00, 0x00 };
uint8_t RearLightDisable[8] = { 0x00, 0x00, 0x00 };
volatile uint8_t bmsAlive[4];  // Read from 0x60C message sent by BMS


//volatile bool testPercentCountUp = true;
//volatile int8_t testPercent = 0;

#define VoltageEmpty 30000
#define VoltageFull 41000
volatile uint16_t cellVoltages[10] = { 0x00, 0x00, 0x00, 0x00, 0x00, 0x00, 0x00, 0x00, 0x00, 0x00 };

volatile double TorqueOutputMax = 900L;
#define TorqueOutputReference 800L

// https://deepbluembedded.com/esp32-timers-timer-interrupt-tutorial-arduino-ide/
hw_timer_t* twoMSTimer = NULL;
volatile uint16_t timerCounter;
#define timerCounterMax 5000
#define timerIntervalMS 2

// ADC Filtering
#define FILTER_LEN 50
volatile uint8_t filterIndex = 0;

uint32_t ThrottleA_Buffer[FILTER_LEN] = { 0 };
uint32_t ThrottleB_Buffer[FILTER_LEN] = { 0 };
uint32_t BrakeR_Buffer[FILTER_LEN] = { 0 };
uint32_t BrakeL_Buffer[FILTER_LEN] = { 0 };

#define ThrottleAADCMin 1100
#define ThrottleAADCMax 3100
#define ThrottleBADCMin 1100
#define ThrottleBADCMax 3100
#define ThrottlePositionCount 1000

#define BrakeRADCMin 1100
#define BrakeRADCMax 2300
#define BrakeLADCMin 1050
#define BrakeLADCMax 2000
#define BrakePositionCount 255

volatile uint32_t ThrottleAFiltered = 0;
volatile uint32_t ThrottleBFiltered = 0;
volatile uint32_t BrakeRFiltered = 0;
volatile uint32_t BrakeLFiltered = 0;

volatile bool timeToRedraw = false;


uint32_t readADC_Avg(uint8_t pinNumber, uint32_t buffer[], uint32_t adcMin, uint32_t adcMax, uint32_t outputMax) {
  // Read and Average
  int i = 0;
  uint32_t Sum = 0;
  uint32_t raw = analogRead(pinNumber);
  //Serial.print("Raw: ");
  //Serial.println(raw);


  buffer[filterIndex] = raw;
  for (i = 0; i < FILTER_LEN; i++) {
    Sum += buffer[i];
  }
  auto avg = Sum / FILTER_LEN;

  // If a range is specified
  if (adcMin != 0 || adcMax != 0) {
    // We have a range
    // Ensure it's within limits
    if (avg < adcMin) return 0;               // We can short-circuit here since if the average is below the minimum, the result is certain to be zero.
    else if (avg > adcMax) return outputMax;  // We can also shortcircuit here for the same reason.

    // Here's where the real calculations happen. We have a number between two numbers,
    // and we need to calculate where it is between those two numbers on a scale of 0 to `outputMax`
    return (avg - adcMin) * outputMax / (adcMax - adcMin);

  } else {
    // No range defined. Return the raw average.
    return avg;
  }
}


void loop() {
  // Read our analog inputs
  ThrottleAFiltered = readADC_Avg(THROTTLEA_PIN, ThrottleA_Buffer, ThrottleAADCMin, ThrottleAADCMax, ThrottlePositionCount);
  ThrottleBFiltered = 1000 - readADC_Avg(THROTTLEB_PIN, ThrottleB_Buffer, ThrottleBADCMin, ThrottleBADCMax, ThrottlePositionCount);
  BrakeRFiltered = readADC_Avg(BRAKER_PIN, BrakeR_Buffer, BrakeRADCMin, BrakeRADCMax, BrakePositionCount);
  BrakeLFiltered = readADC_Avg(BRAKEL_PIN, BrakeL_Buffer, BrakeLADCMin, BrakeLADCMax, BrakePositionCount);

  filterIndex++;
  if (filterIndex == FILTER_LEN) {
    filterIndex = 0;
  }
/*
  if (Serial.available() >= 3) {
    Serial.setTimeout(10);
    testPercent = Serial.parseInt();
    timeToRedraw = true;
    Serial.setTimeout(1000);
  }*/

  if (timeToRedraw) {
    RedrawScreen();
    timeToRedraw = false;
  }
  // TODO: Based on the two values, Figure out if the throttle has borked, and do something sensible
  throttlePos = ThrottleAFiltered;
  StartStopDebouncer.debounce(digitalRead(START_STOP_PIN));

  if (StartStopDebouncer.falling()) {
    //screenServer();

    if (!driver_installed) {

      // Initialize configuration structures using macro initializers
      twai_general_config_t g_config = TWAI_GENERAL_CONFIG_DEFAULT((gpio_num_t)CAN_TX_PIN, (gpio_num_t)CAN_RX_PIN, TWAI_MODE_NO_ACK);
      twai_timing_config_t t_config = TWAI_TIMING_CONFIG_500KBITS();  //Look in the api-reference for other speed sets.
      twai_filter_config_t f_config = TWAI_FILTER_CONFIG_ACCEPT_ALL();

      // Default scooter state to disabled.
      RemoteXY.ScooterState = 1;
      // Install TWAI driver
      if (twai_driver_install(&g_config, &t_config, &f_config) == ESP_OK) {
        Serial.println("Driver installed");
      } else {
        Serial.println("Failed to install driver");
        //return;
      }
      // Start TWAI driver
      if (twai_start() == ESP_OK) {
        Serial.println("Driver started");
        // TWAI driver is now successfully installed and started
        driver_installed = true;
      } else {
        Serial.println("Failed to start driver");
      }


      // Setup the timer https://deepbluembedded.com/esp32-timers-timer-interrupt-tutorial-arduino-ide/
      twoMSTimer = timerBegin(0, 80, true);
      timerAttachInterrupt(twoMSTimer, &Timer0_ISR, false);
      timerAlarmWrite(twoMSTimer, timerIntervalMS * 1000, true);
      timerAlarmEnable(twoMSTimer);
    } else {
      // If user has selected to enable the brake, the button doesn't enable the scooter.
      if (scooterState == Idle) {
        scooterState = Running;
        updateColor(0, 255, 0);
        digitalWrite(HEADLIGHT_PIN, HIGH);
#ifdef LCD_BL_SIG
        ledcWrite(4, 255);
#endif

      } else if (scooterState == Running) {
        scooterState = Idle;
        updateColor(255, 0, 0);
        digitalWrite(HEADLIGHT_PIN, LOW);
#ifdef LCD_BL_SIG
        ledcWrite(4, 30);
#endif
      }
    }
  }

  if (driver_installed) {
    //Wait for message to be received
    twai_message_t message;
    if (twai_receive(&message, pdMS_TO_TICKS(0)) == ESP_OK) {
      if (message.identifier == 0x60C) {
        // Read BMS ID message used for keepalive
        bmsAlive[0] = message.data[0];
        bmsAlive[1] = message.data[1];
        bmsAlive[2] = message.data[2];
        bmsAlive[3] = message.data[3];
      } else if (0x701 <= message.identifier && message.identifier <= 0x70A) {
        // Read cell voltage
        uint16_t voltage = message.data[0] | message.data[1] << 8;
        cellVoltages[message.identifier - 0x701] = voltage;
      } else if (message.identifier == 0x152) {
        currentSpeed = message.data[2] | message.data[3] << 8;
      }
    } else {
      //Serial.println("Failed to receive message");
    }

    RemoteXY_Handler();
    switch (RemoteXY.ScooterState) {
      case 0:  // Enable
        if (!(scooterState == Idle || scooterState == Running)) {
          Serial.println("Set Idle");
          scooterState = Idle;
        }
        break;
      case 1:  // Disable
        if (scooterState != Disabled) {
          Serial.println("Set Disabled");
          scooterState = Disabled;
          digitalWrite(HEADLIGHT_PIN, LOW);
#ifdef LCD_BL_SIG
          ledcWrite(4, 30);
#endif
        }
        break;
      case 2:  // Lock
        if (scooterState != LockWheel) {
          Serial.println("Set Lock");
          scooterState = LockWheel;
          digitalWrite(HEADLIGHT_PIN, LOW);
#ifdef LCD_BL_SIG
          ledcWrite(4, 30);
#endif
        }
        break;
    }
  }
}

// Used if there's an RGB LED
void updateColor(uint8_t R, uint8_t G, uint8_t B) {
#ifdef ledR
  // write the RGB values to the pins
  ledcWrite(1, 255 - R);  // write red component to channel 1, etc.
  ledcWrite(2, 255 - G);
  ledcWrite(3, 255 - B);
#endif
}

void sendCANMessage(uint32_t identifier, uint8_t length, uint8_t data[]) {
  if (driver_installed) {
    // Configure message to transmit
    twai_message_t message;
    message.extd = 0;
    message.flags = 0;
    message.rtr = 0;
    message.identifier = identifier;
    message.data_length_code = length;
    for (int i = 0; i < length; i++) {
      message.data[i] = data[i];
    }
    auto result = twai_transmit(&message, pdMS_TO_TICKS(1) / 100);
    // Queue message for transmission
    if (result != ESP_OK) {
      Serial.print("Failed to queue message for transmission: ");
      Serial.println(result);
    }
  }
}

void sendMotorTorque() {

  union {
    uint32_t x;
    byte myData[4];  //little endian
  } data;

  data.x = 0;
  if (scooterState == Running) {
    if (BrakeRFiltered > 0) {
      data.x = BrakeRFiltered << 16;
    } else if (throttlePos > 0) {
      double throttleF = pow((double)throttlePos, 2.2L) / 5700L;
      throttleF = throttleF * TorqueOutputMax / TorqueOutputReference;
      data.x = lround(throttleF);
    }
  } else if (scooterState == LockWheel) {
    data.x = 0x01 << 24;
  }
  sendCANMessage(0x153, 4, data.myData);
}

void sendKeepAlive() {
  if (driver_installed) {
    if (uptime % 1 == 0) {
      byte keepAlive[8] = {
        (uint8_t)(uptime & 0xFF),
        (uint8_t)((uptime >> 8) & 0xFF),
        (uint8_t)((uptime >> 16) & 0xFF),
        (uint8_t)((uptime >> 24) & 0xFF),
        (uint8_t)bmsAlive[0],
        (uint8_t)bmsAlive[1],
        (uint8_t)bmsAlive[2],
        (uint8_t)bmsAlive[3]
      };

      sendCANMessage(0x742, 8, keepAlive);
    }
    uptime++;
  }
}

void sendBMSEnable() {
  // When the state changes to no longer enable BMS, keep BMS enabled for 120 seconds.
  // If the BMS is disabled, it refuses to re-enable itself for 10 - 20 seconds, and this delay
  // gives the user a chance to change their mind.
  if (scooterState == Running || scooterState == LockWheel) {
    sendCANMessage(0x140, 8, BMSOutputEnable);
    bmsOutputDisableRequestedUptime = 0;
  } else if ((bmsOutputDisableRequestedUptime > 0 && uptime - bmsOutputDisableRequestedUptime < 120)) {
    sendCANMessage(0x140, 8, BMSOutputEnable);
  } else {
    if (bmsOutputDisableRequestedUptime == 0) {
      // First loop where enable no longer requested.
      bmsOutputDisableRequestedUptime = uptime;
      sendCANMessage(0x140, 8, BMSOutputEnable);
    } else {
      sendCANMessage(0x140, 8, BMSOutputDisable);
    }
  }
}

void sendRearLight() {
  if (scooterState == Running) {
    sendCANMessage(0x500, 3, RearLightEnable);
  } else {
    sendCANMessage(0x500, 3, RearLightDisable);
  }
}

void sendDebugVariables() {
  /*
  Serial.print("Bottom:0 Top:4000 ThrottleA:");
  Serial.print(ThrottleAFiltered);
  Serial.print("  ThrottleB:");
  Serial.print(ThrottleBFiltered);
  Serial.print("  BrakeR:");
  Serial.print(BrakeRFiltered);
  Serial.print("  BrakeL:");
  Serial.println(BrakeLFiltered);

  Serial.print("Speed: ");
  Serial.print(currentSpeed);
  Serial.print(" ");
  Serial.print(currentSpeed * SpeedToMPH);
  Serial.print("mph ");
  Serial.print(currentSpeed * SpeedToKPH);
  Serial.println("kph ");*/
}

void DrawCenteredString(const char* text, OpenFontRender& font, uint16_t size, uint16_t color, uint16_t x, uint16_t y, uint16_t w, uint16_t h) {
  TFT_eSprite spr = TFT_eSprite(&tft);
  spr.createSprite(w, h);
  spr.setColorDepth(16);
  font.setDrawer(spr);

  font.setFontSize(size);
  font.setAlignment(Align::TopLeft);
  FT_BBox textSize = font.calculateBoundingBox(0, 0, size, Align::TopLeft, Layout::Horizontal, text);
  font.drawString(text, w / 2 - (textSize.xMax - textSize.xMin) / 2 - textSize.xMin, h / 2 - (textSize.yMax - textSize.yMin) / 2 - textSize.yMin, color, TFT_BLACK, Layout::Horizontal);

  spr.pushToSprite(&screen, x, y, TFT_BLACK);
  spr.deleteSprite();
}

void RedrawScreen() {
  screen.fillScreen(TFT_BLACK);

  // Calculate Battery Percentage
  bool voltageTBD = false;
  double totalVoltage = 0;
  for (uint8_t i = 0; i < 10; i++) {
    //Serial.println(cellVoltages[i]);
    if (cellVoltages[i] == 0) {
      // Zero indicates we haven't received one of the cell voltages yet, so rather than showing a partial voltage, just display `TBD...`
      voltageTBD = true;
      break;
    }
    totalVoltage += cellVoltages[i];
  }

  // Debug stuff
  //voltageTBD = false;
  //totalVoltage = 42000;

  uint16_t batteryBorder;
  uint16_t batteryFill;
  String batteryString;
  int16_t batteryPercent;
  if (voltageTBD) {
    batteryBorder = tft.color565(0xFF, 0xFF, 0xFF);
    batteryFill = tft.color565(0x00, 0x00, 0x00);
    batteryString = String("TBD...");
    batteryPercent = 0;
  } else {
    batteryPercent = (int16_t)((totalVoltage - VoltageEmpty) / (VoltageFull - VoltageEmpty) * 100);
    batteryPercent = min(batteryPercent, (int16_t)100);
    //batteryPercent = testPercent;
    batteryString = String(batteryPercent);
    batteryString.concat("%");
    if (batteryPercent > 20) {
      batteryBorder = TFT_GREEN;
      batteryFill = TFT_DARKGREEN;
    } else if (batteryPercent < 5) {
      batteryBorder = tft.color565(0xFF, 0x00, 0x00);
      batteryFill = tft.color565(0x7F, 0x00, 0x00);
    } else {
      batteryBorder = tft.color565(0xFF, 0xD8, 0x00);
      batteryFill = tft.color565(0xA8, 0x8C, 0x00);
    }
  }


#define FillX 8
#define FillY 8
#define FillWidth 225
#define FillHeight 45
#define FillRadius 9

  if (batteryPercent > 0) {  // Don't bother drawing
    // Draw internal rounded border of the fill
    screen.fillSmoothRoundRect(FillX, FillY, FillWidth, FillHeight, FillRadius, batteryFill, batteryBorder);
    // Erase the part of the bar that we don't want. This allows us to precisely remove the part we don't want
    uint8_t PixelsToErase = FillWidth * (100 - batteryPercent) / 100;
    screen.fillRect(FillX + FillWidth - PixelsToErase, FillY, PixelsToErase, FillHeight, TFT_BLACK);
  }
  // Draw border
  screen.drawSmoothRoundRect(5, 5, 11, 9, 230, 50, batteryBorder, batteryFill, 0xF);
  DrawCenteredString(batteryString.c_str(), noto, 80, TFT_WHITE, 0, 4, 240, 50);

  if (scooterState == Idle || scooterState == Running) {
    // Speed
    int8_t speed = (((double)currentSpeed) * SpeedToMPH);
    DrawCenteredString(String(speed).c_str(), noto, 330, scooterState == Idle ? TFT_RED : TFT_WHITE, 0, 60, 240, 140);
    DrawCenteredString("mph", noto, 50, scooterState == Idle ? TFT_RED : TFT_WHITE, 0, 200, 240, 40);
  } else {
    DrawCenteredString("l", icons, 130, scooterState == LockWheel ? TFT_RED : TFT_WHITE, 0, 60, 240, 140);
  }
  tft.setSwapBytes(false);
  screen.pushSprite(0, 0);
  tft.setSwapBytes(true);
}

void IRAM_ATTR Timer0_ISR() {
  // This timer runs every 2ms in order to send the current motor speed.
  // There are other things we need to do, but since the ESP32 has a limited
  // number of timers, we don't wish to use them all for the various messages
  // we need to send at different intervals. Instead, we simply increment a
  // variable and check if it's divisible by the desired interval.

  sendMotorTorque();

  // Every 50 ms
  if (timerCounter % 50 == 0) {
    sendRearLight();
    //sendDebugVariables();
  }

  // Every 200 ms
  if (timerCounter % 200 == 0) {
    sendBMSEnable();
    sendDebugVariables();
    /*
    if (testPercentCountUp) {
      testPercent++;
      if (testPercent >= 100) {
        testPercentCountUp = false;
      }
    } else {
      testPercent--;
      if (testPercent <= -20) {
        testPercentCountUp = true;
      }
    }*/
    timeToRedraw = true;
  }

  // Every 1000 ms
  if (timerCounter % 1000 == 0) {
    sendKeepAlive();
    uint16_t totalVoltage = 0;
    uint8_t i;
    for (i = 0; i < 10; i++) {
      totalVoltage += cellVoltages[i];
    }

    //Serial.print("Battery Voltage: ");
    //Serial.print(totalVoltage);
    //Serial.println("mv");
  }

  timerCounter += timerIntervalMS;
  if (timerCounter >= timerCounterMax) {
    timerCounter = 0;
  }
}



void setup() {
  Serial.begin(921600);
  Serial.println("Started Serial");
  analogReadResolution(12);
  RemoteXY_Init();
  RemoteXY.ScooterState = 1;
  // Configure the Start/Stop button
  pinMode(START_STOP_PIN, INPUT_PULLUP);
  StartStopDebouncer.mode(DELAYED, 10, false);

  // Configure the headlight pin
  pinMode(HEADLIGHT_PIN, OUTPUT);
#ifdef PWR_ENA_SIG
  pinMode(PWR_ENA_SIG, OUTPUT);
  digitalWrite(PWR_ENA_SIG, HIGH);
#endif
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

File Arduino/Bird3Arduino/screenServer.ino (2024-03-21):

/*/ Reads a screen image off the TFT and send it to a processing client sketch
// over the serial port. Use a high baud rate, e.g. for an ESP8266:
// Serial.begin(921600);

// At 921600 baud a 320 x 240 image with 16-bit colour transfers can be sent to the
// PC client in ~1.67s and 24-bit colour in ~2.5s which is close to the theoretical
// minimum transfer time.

// This sketch has been created to work with the TFT_eSPI library here:
// https://github.com/Bodmer/TFT_eSPI

// Created by: Bodmer 27/1/17
// Updated by: Bodmer 10/3/17
// Updated by: Bodmer 23/11/18 to support SDA reads and the ESP32
// Version: 0.08

// MIT licence applies, all text above must be included in derivative works

//====================================================================================
//                                  Definitions
//====================================================================================
#define PIXEL_TIMEOUT 100     // 100ms Time-out between pixel requests
#define START_TIMEOUT 10000   // 10s Maximum time to wait at start transfer

#define BITS_PER_PIXEL 16     // 24 for RGB colour format, 16 for 565 colour format

// File names must be alpha-numeric characters (0-9, a-z, A-Z) or "/" underscore "_"
// other ascii characters are stripped out by client, including / generates
// sub-directories
#define DEFAULT_FILENAME "tft_screenshots/screenshot" // In case none is specified
#define FILE_TYPE "png"       // jpg, bmp, png, tif are valid

// Filename extension
// '#' = add incrementing number, '@' = add timestamp, '%' add millis() timestamp,
// '*' = add nothing
// '@' and '%' will generate new unique filenames, so beware of cluttering up your
// hard drive with lots of images! The PC client sketch is set to limit the number of
// saved images to 1000 and will then prompt for a restart.
#define FILE_EXT  '@'         

// Number of pixels to send in a burst (minimum of 1), no benefit above 8
// NPIXELS values and render times:
// NPIXELS 1 = use readPixel() = >5s and 16-bit pixels only
// NPIXELS >1 using rectRead() 2 = 1.75s, 4 = 1.68s, 8 = 1.67s
#define NPIXELS 1  // Must be integer division of both TFT width and TFT height

//====================================================================================
//                           Screen server call with no filename
//====================================================================================
// Start a screen dump server (serial or network) - no filename specified
bool screenServer(void)
{
  // With no filename the screenshot will be saved with a default name e.g. tft_screen_#.xxx
  // where # is a number 0-9 and xxx is a file type specified below
  return screenServer(DEFAULT_FILENAME);
}

//====================================================================================
//                           Screen server call with filename
//====================================================================================
// Start a screen dump server (serial or network) - filename specified
bool screenServer(String filename)
{
  delay(0); // Equivalent to yield() for ESP8266;

  bool result = serialScreenServer(filename); // Screenshot serial port server
  //bool result = wifiScreenServer(filename);   // Screenshot WiFi UDP port server (WIP)

  delay(0); // Equivalent to yield()

  //Serial.println();
  //if (result) Serial.println(F("Screen dump passed :-)"));
  //else        Serial.println(F("Screen dump failed :-("));

  return result;
}

//====================================================================================
//                Serial server function that sends the data to the client
//====================================================================================
bool serialScreenServer(String filename)
{
  // Precautionary receive buffer garbage flush for 50ms
  uint32_t clearTime = millis() + 50;
  while ( millis() < clearTime && Serial.read() >= 0) delay(0); // Equivalent to yield() for ESP8266;

  bool wait = true;
  uint32_t lastCmdTime = millis();     // Initialise start of command time-out

  // Wait for the starting flag with a start time-out
  while (wait)
  {
    delay(0); // Equivalent to yield() for ESP8266;
    // Check serial buffer
    if (Serial.available() > 0) {
      // Read the command byte
      uint8_t cmd = Serial.read();
      // If it is 'S' (start command) then clear the serial buffer for 100ms and stop waiting
      if ( cmd == 'S' ) {
        // Precautionary receive buffer garbage flush for 50ms
        clearTime = millis() + 50;
        while ( millis() < clearTime && Serial.read() >= 0) delay(0); // Equivalent to yield() for ESP8266;

        wait = false;           // No need to wait anymore
        lastCmdTime = millis(); // Set last received command time

        // Send screen size etc.using a simple header with delimiters for client checks
        sendParameters(filename);
      }
    }
    else
    {
      // Check for time-out
      if ( millis() > lastCmdTime + START_TIMEOUT) return false;
    }
  }

  uint8_t color[3 * NPIXELS]; // RGB and 565 format color buffer for N pixels

  // Send all the pixels on the whole screen
  for ( uint32_t y = 0; y < tft.height(); y++)
  {
    // Increment x by NPIXELS as we send NPIXELS for every byte received
    for ( uint32_t x = 0; x < tft.width(); x += NPIXELS)
    {
      delay(0); // Equivalent to yield() for ESP8266;

      // Wait here for serial data to arrive or a time-out elapses
      while ( Serial.available() == 0 )
      {
        if ( millis() > lastCmdTime + PIXEL_TIMEOUT) return false;
        delay(0); // Equivalent to yield() for ESP8266;
      }

      // Serial data must be available to get here, read 1 byte and
      // respond with N pixels, i.e. N x 3 RGB bytes or N x 2 565 format bytes
      if ( Serial.read() == 'X' ) {
        // X command byte means abort, so clear the buffer and return
        clearTime = millis() + 50;
        while ( millis() < clearTime && Serial.read() >= 0) delay(0); // Equivalent to yield() for ESP8266;
        return false;
      }
      // Save arrival time of the read command (for later time-out check)
      lastCmdTime = millis();
  //tft.setSwapBytes(false);
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

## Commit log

2023-10-07 Add .net Windows Forms application to unlock battery and control motor.
2023-10-08 Add basic sketch to use hardware timers and read the throttle.
2023-10-14 It works! A bunch has changed: It actually operates the scooter, there's a button to turn it off and on, an output for the headlight LED, and another set of keepalive messages for the EA00022 control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
2023-12-19 Delay the canbus initialization until the first button press to allow connecting the debug serial
2024-01-22 Reset back to 0 when it would reach timerCounterMax rather than after it reaches it.
    Because: timerCounterMax = 5000. Tthe old logic resulted in events being processed when timerCounter equaled 5000 *and* when it equaled 0. This caused those events to be run double every five seconds.
    [Bird3Arduino.ino]
2024-01-22 Receive the 0x60C message and use it to keep the BMS awake
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2024-03-07 Read the messages for battery voltage and wheel/motor speed.
2024-03-07 Send braking message when right brake is pulled. It doesn't work yet, but it's here.
    [Bird3Arduino.ino]
2024-03-08 Add kicad PCB
    [Bird3Controller.kicad_pcb, Bird3Controller.kicad_sch]
2024-03-21 Add prototype schematic
    [Bird3Controller.kicad_pcb, Bird3Controller.kicad_sch]
2024-03-21 Support the custom Bird Brain board Revision 1
2024-03-21 Add datasheets
    [24-pin Connector Pinout.xlsx]
2024-03-21 Final Rev1 schematic update
    [Bird3Controller.kicad_sch]
2024-03-21 Add components excel
    [components.xlsx]
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2024-03-21 Copy Rev1 for Rev2
    [Bird3Controller-B_Cu.gbl, Bird3Controller-B_Mask.gbs, Bird3Controller-B_Paste.gbp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]
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2024-03-21 Move Revision 1 to a more clearly named directory
    [Bird3Controller.kicad_pcb, Bird3Controller.kicad_sch, components.xlsx]
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2024-03-22 Reduce keepalive interval to 1 second to attempt keeping the BMS from sleeping
2024-03-28 Add 22-pin connector, new headlight circuit, etc. for Rev 2
    [Bird3Controller.kicad_pcb, Bird3Controller.kicad_sch]
2024-03-30 Add circuit to selectively ground the `PWR_ENA` pin
    [Bird3Controller.kicad_pcb, Bird3Controller.kicad_sch]
2024-03-30 Add `PWR_ENA` mosfet and fuse to PCB
    [Bird3Controller.kicad_pcb]
2024-03-30 Update PCB to use add PTC fuse on VIN
    [Bird3Controller.kicad_pcb, Bird3Controller.kicad_sch]
2024-03-30 Label USB connector pins
    [Bird3Controller.kicad_pcb]
2024-03-30 Rearrange some things to remove some vias
    [Bird3Controller.kicad_pcb]
2024-03-30 Upgrade Rev2 project and files to KiCad 8 using KiCad 8.0.1
    [Bird3Controller.kicad_pcb, Bird3Controller.kicad_sch]
2024-03-30 Adjust edge.cuts on the PCB and in the LCD connector footprint to remove overlapping lines that were creating trouble.
    [Bird3Controller.kicad_pcb]
2024-03-30 Update PCB from schematic for first time since v8
    [Bird3Controller.kicad_pcb, Bird3Controller.kicad_sch]
2024-03-30 Add EEPROM to schematic and board.
    Also add the symbol, footprint, and 3D model
    [Bird3Controller.kicad_pcb, Bird3Controller.kicad_sch]
2024-03-30 Fix silkscreen for USB breakout header
    [Bird3Controller.kicad_pcb]
2024-03-30 Move things around to eliminate two vias in the CAN_TX trace
    [Bird3Controller.kicad_pcb]
2024-03-30 Push more things around
    [Bird3Controller.kicad_pcb]
2024-03-30 Move vias around a bit
    [Bird3Controller.kicad_pcb]
2024-03-30 Don't use thermal relief for SMD components
    [Bird3Controller.kicad_pcb]
2024-03-30 Add more ground-plane vias
    [Bird3Controller.kicad_pcb]
2024-03-30 Push LCD data traces around and add more ground plane vias
    [Bird3Controller.kicad_pcb]
2024-03-30 Add silkscreen reference to github repo and a placement for the JLCPCB order number
    [Bird3Controller.kicad_pcb]
2024-03-30 Update gerbers and rendering for Revision 2
    [Bird3Controller-B_Cu.gbl, Bird3Controller-B_Mask.gbs, Bird3Controller-B_Paste.gbp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]
2024-03-30 Add Mouser links and prices for all components
    [Bird3Controller.kicad_sch]
2024-03-30 Add Bill of Materials
    [BOM.csv]
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2024-04-06 If `PWR_ENA_SIG` is defined, write an output to that pin to activate the mosfet to pull the `PWR_ENA` pin to ground.
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2024-04-06 Add background to symbols for consistency
    [Bird3Controller.kicad_sch]
2024-04-06 Update schematic revision number
    [Bird3Controller.kicad_sch]
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2024-04-06 Update fields on PCB
    [Bird3Controller.kicad_pcb]
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2024-04-06 Fix part number that referred to 0.402ohm resistor instead of the correct 0.200ohm value
    [BOM.csv, Bird3Controller.kicad_pcb, Bird3Controller.kicad_sch]
2024-04-06 Correct LCD rotation for Rev 2
    [Bird3Arduino.ino]
2024-04-14 Add Revision 3
    [Bird3Controller.kicad_pcb, Bird3Controller.kicad_sch]
2024-04-14 Rearrange schematic
    [Bird3Controller.kicad_sch]
2024-04-14 Optimize ground plane/vias
    [Bird3Controller.kicad_pcb]
2024-04-15 Shrink LCD Connector pads to reduce bridging
    [Bird3Controller.kicad_pcb]
2024-04-15 Switch to thermal reliefs for pad connections except for thermal pads. Also move some traces around to optimize the thermal reliefs
    [Bird3Controller.kicad_pcb]
2024-04-15 Rearrange and add ground plane vias
    [Bird3Controller.kicad_pcb]
2024-04-15 Correct ESP32 thermal pad violations and the USB-C breakout text that keeps moving randomly
    [Bird3Controller.kicad_pcb]
2024-04-15 Update footprints to better indicate pin 1
    [Bird3Controller.kicad_pcb]
2024-04-15 Add test points
    [Bird3Controller.kicad_pcb, Bird3Controller.kicad_sch]
2024-04-16 Add Rev3 Gerbers
    [Bird3Controller-B_Cu.gbl, Bird3Controller-B_Mask.gbs, Bird3Controller-B_Paste.gbp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]
2024-04-16 Add missing test point names on silkscreen.
    [Bird3Controller.kicad_pcb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]
2024-04-17 Add `Rating` field, use lower cost VIN cap, add description to most components
    [Bird3Controller.kicad_pcb, Bird3Controller.kicad_sch]
2024-04-17 Add Revision 3 BOM
    [BOM.csv]
2024-04-25 Add basic RemoteXY BLE security. Add custom font with lock icon. Add enumeration for state and delay disabling BMS.
2024-05-05 Fix R12 and R13 label position
    [Bird3Controller.kicad_pcb]
2024-05-05 Rename fields to work with `kicost`. Also, correct the Mouser Part Number for C15.
    [Bird3Controller.kicad_pcb, Bird3Controller.kicad_sch]
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
